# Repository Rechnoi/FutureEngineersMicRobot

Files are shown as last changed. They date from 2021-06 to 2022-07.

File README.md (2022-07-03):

# Команда Violet
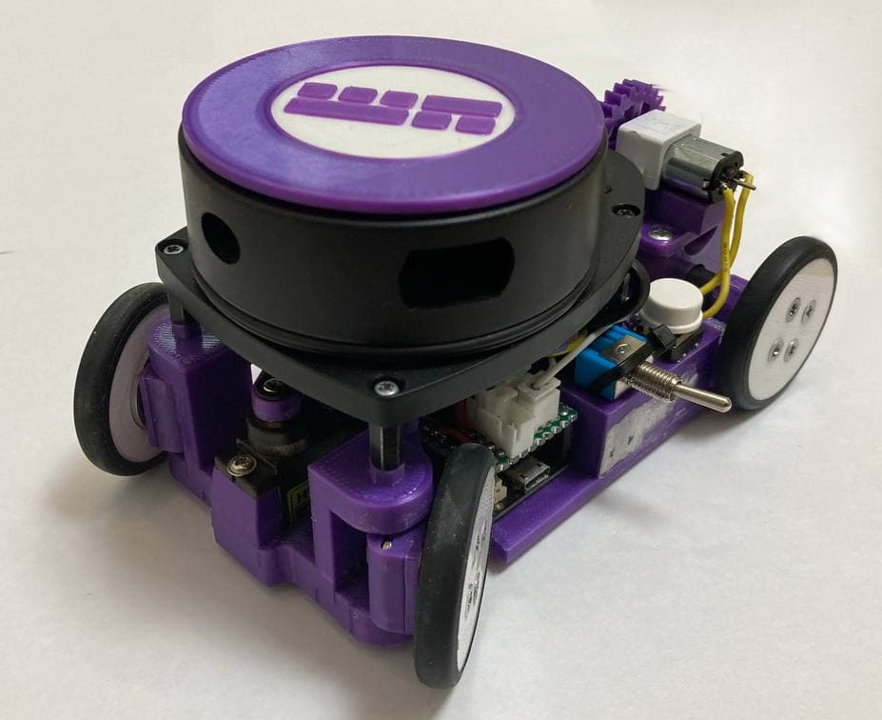
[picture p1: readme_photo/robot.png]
General


### Робот, созданный для решения задачи WRO FutureEngineers 2022 (Version Mk. IV)
### © Антон Иванченко, Александр Широковских, Дмитрий Шмелёв

<br>

## Наш видеообзор на [Youtube](https://youtu.be/LUYHc2npUGY)

<br>

## Введение
  Перед нами стояла задача спроектировать и собрать беспилотное транспортное средство, которое могло бы верно и точно выполнить задачу WRO FutureEngineers 2022. Для достижения поставленных целей мы построили четырехколесного робота на базе ESP32. Основными датчикомами этого робота стали лидар и камер, которые дают информацию о расстоянии до объектов вокруг робота и цвете знаков перед роботом. При разработке были учтены геометрические особенности транспортных средств, такие как углы Аккермана и дифференциальная передача момента.

## Содержание репозитория
  - Папка "3D-models" содержит все версии робота
  - Папка "final/main" содержит код финального заезда
  - Папка "qual/main" содержит код для квалификационного заезда
  - Папка "schematic" содержит электромеханическую схему робота
  - Папка "team_photo" содержит два фото команды по регламенту
  - Папка "robot_photo" содержит обзорные фото робота с шести сторон
  - Папка "readme_photo" содержит фото, используемые в README.md файле

## Фото робота
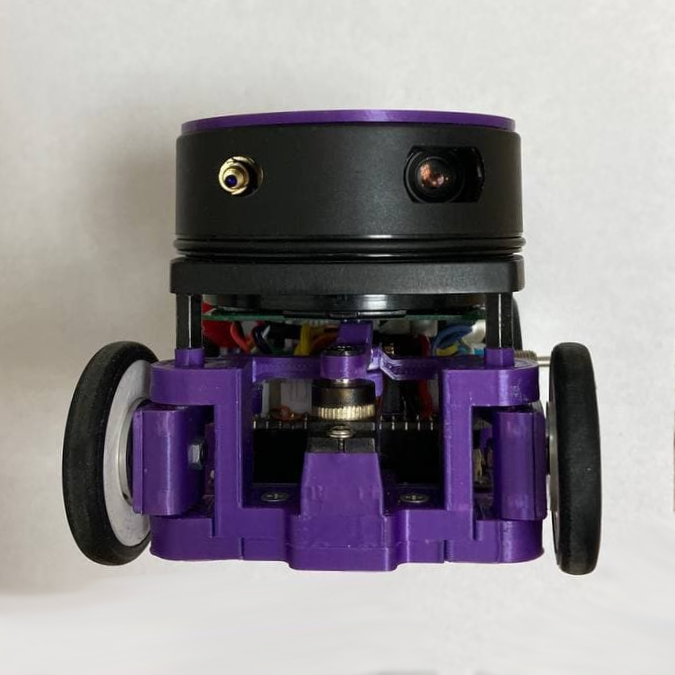
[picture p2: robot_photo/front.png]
Front
  
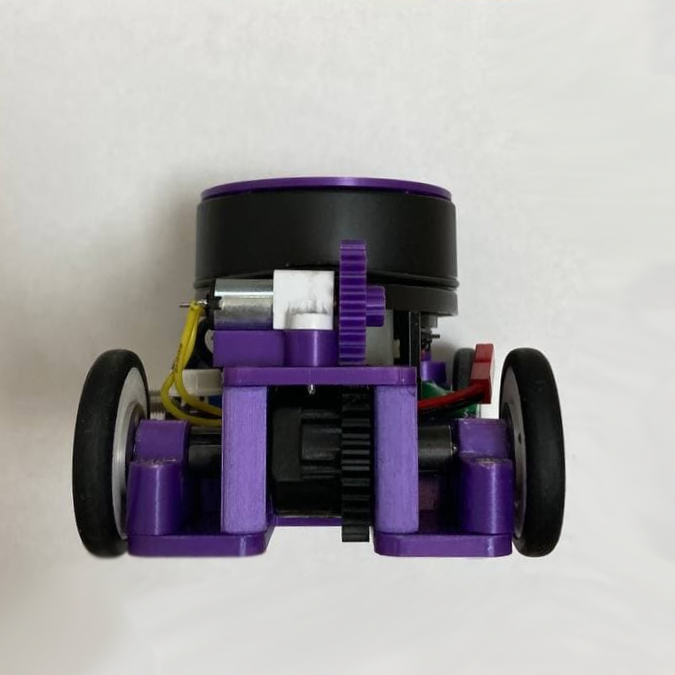
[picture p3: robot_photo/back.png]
Back
  
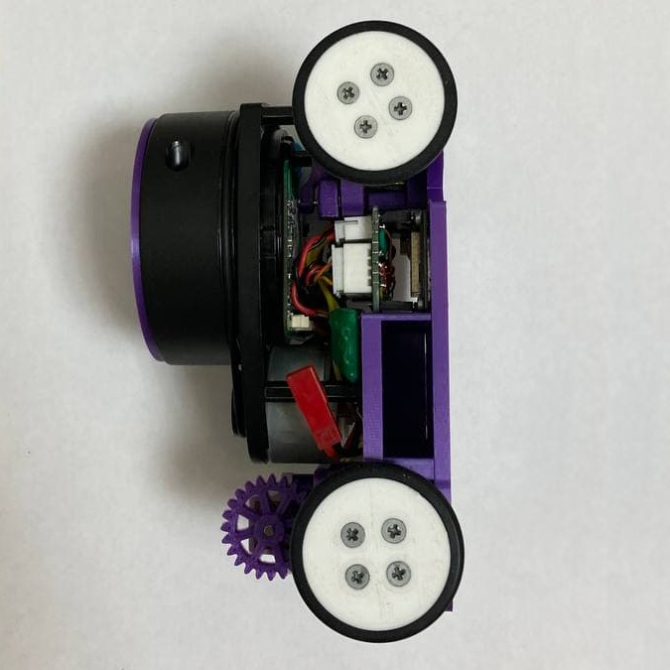
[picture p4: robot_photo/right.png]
Right
  
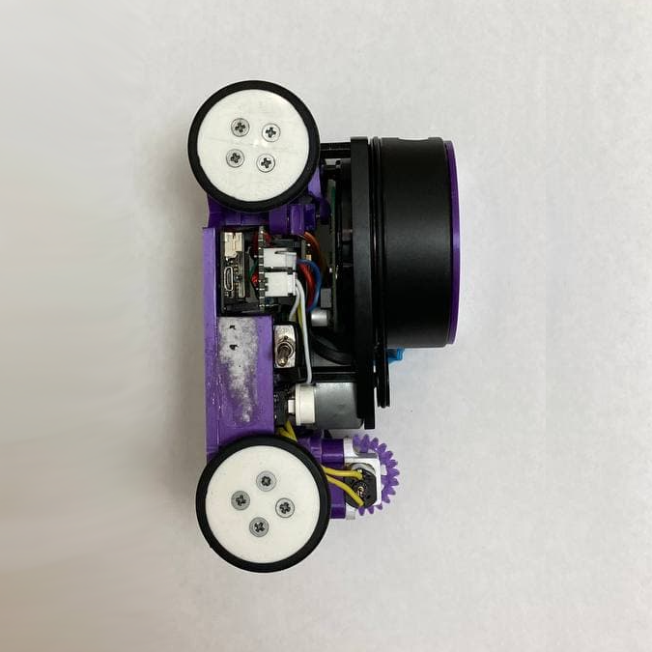
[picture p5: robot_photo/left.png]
Left
  
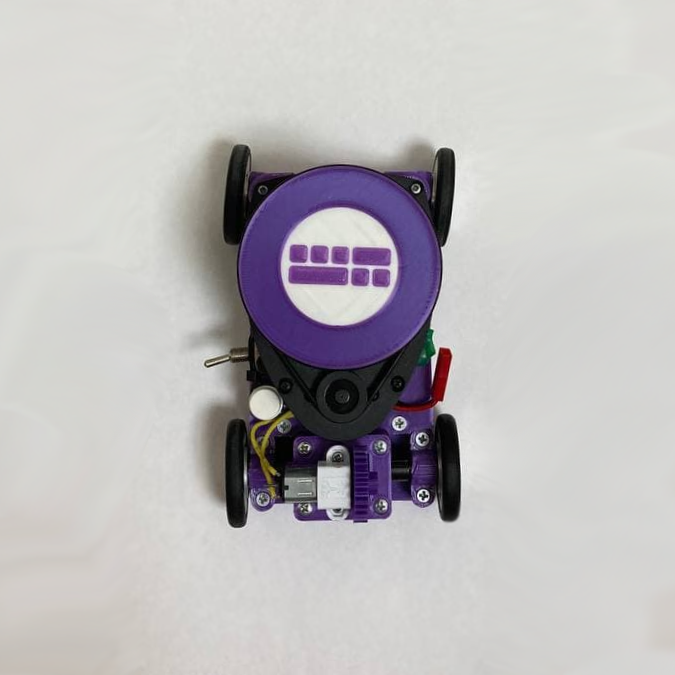
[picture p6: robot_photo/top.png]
Top
  
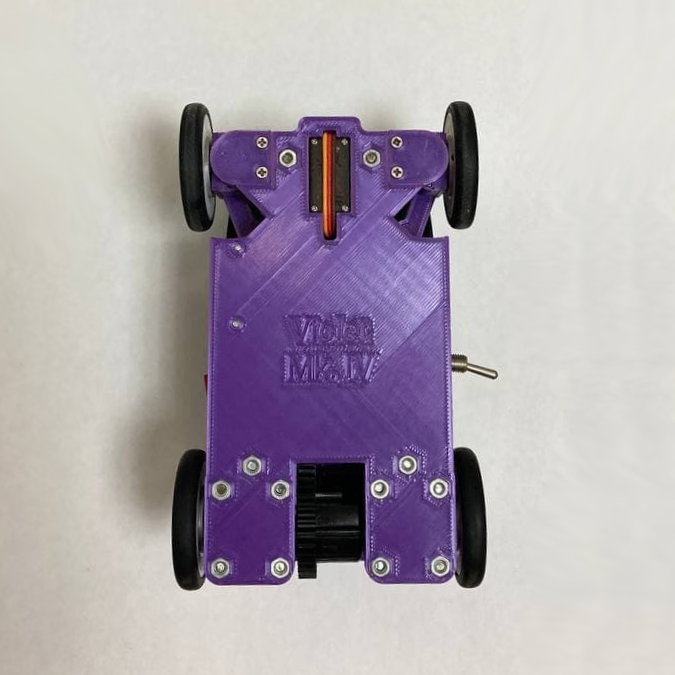
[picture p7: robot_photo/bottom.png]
Bottom
  
  
  *Если картинки не открываются, проверьте папку "robot_photo", пожалуйста

## Схема электромеханического устройства
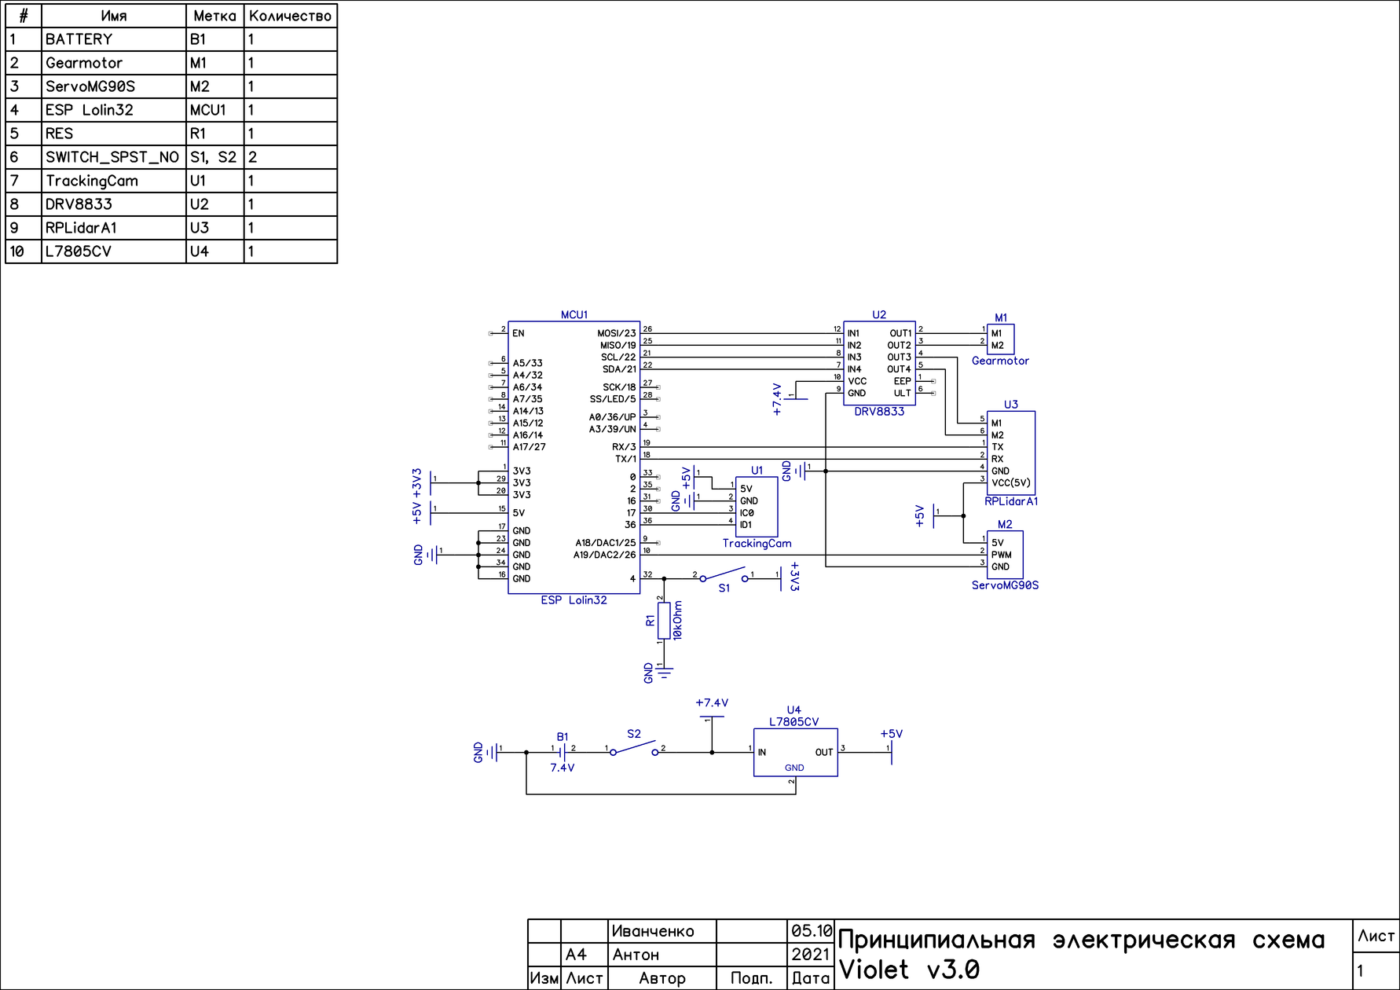
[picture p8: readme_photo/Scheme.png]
Схема
  
  
  *Если картинка не открывается или вам нужна картинка лучшего качества, проверьте папку "schematic", пожалуйста.

## Сборка робота
  - Сначала вам нужно напечатать все необходимые части робота. Для этого зайдите в папку "3D-models/RRO 2021 Mk. IV/STL" и распечатайте все модели на 3D-принтере.
  - Во-вторых, вам нужно купить все необходимые компоненты: [лидар](https://www.slamtec.com/en/Lidar/A1), [камеру](https://robotgeeks.ru/collection/komplektuyuschie-dlya-avtonomnyh-robotov/product/modul-tehnicheskogo-zreniya-trackingcam), [мотор](https://www.pololu.com/product/3042), [сервопривод](https://aliexpress.ru/item/1005002235406689.html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,searchweb201602_,searchweb201603_), [драйвер мотора](https://mcustore.ru/store/moduli/drajver-dvigatelya-drv8833/) и [плату ESP Lolin32](https://mcustore.ru/store/espressif-systems/wemos-loin32-sovmestimyj-kontroller-pod-akkumulyator/), а также компоненты, задействованные в печатной плате робота. Для робота также необходимы 4 подшипника 3x8x3, 2 подшипника 3x8x4, латунные втулки 3x5x4, [дифференциал](https://rc-today.ru/product/differencial-hsp-60065/) и четыре силиконовые [шины Pololu](https://www.pololu.com/product/3408). Для питания робота можно использовать любую 7.4V 2S Li-Po батарею размером 53x30x11.5мм, например, мы используем вот эту [батарею](https://rc-go.ru/cat/akkumulyator-gensace-lipo-7-4v-2s-25c-450mah/).  
  - В-третьих, для сборки напечатаных и купленных компонентов понадобится 12 гаек M3 и 10 гаек М2 гаек и следующие винты(размер указан от головки до конца резьбы):
    - 2xM3 7.6мм (с потайной головкой)
    - 2xM3 20.8мм (с потайной головкой)
    - 2xM3 16.25мм (с потайной головкой)
    - 4xM3 16.25мм (с потайной головкой)
    - 16xM3 6.5мм (с потайной головкой)
    - 4xM3 33.8мм
    - 2xM2 7мм
    - 2xM2 8.8мм
    - 8xM2 6,5мм (с потайной головкой)
    - 6xM2 10мм (с потайной головкой)
  - В-четвертых, в соответствии со схемой, необходимо иметь макетную плату размером не более 55,8x25,4 мм. Рекомендуется использовать штырьевой разъем и гребенку-гнездо для удобства замены сгоревших компонентов. Плата управления должна быть собрана в следующем порядке: ESP Lolin32, плата шилда и драйвер.
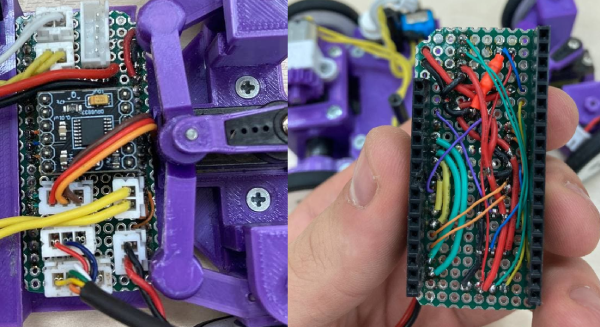
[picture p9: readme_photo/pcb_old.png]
PCB_old
  
  - В-пятых, открыв в Inventor файл-сборку "3D-models/RRO 2021 Mk. IV/Робот RRO 2021 Mk. IV.iam", соберите робота, как показано на модели.

## О наших электрических и механических компонентах
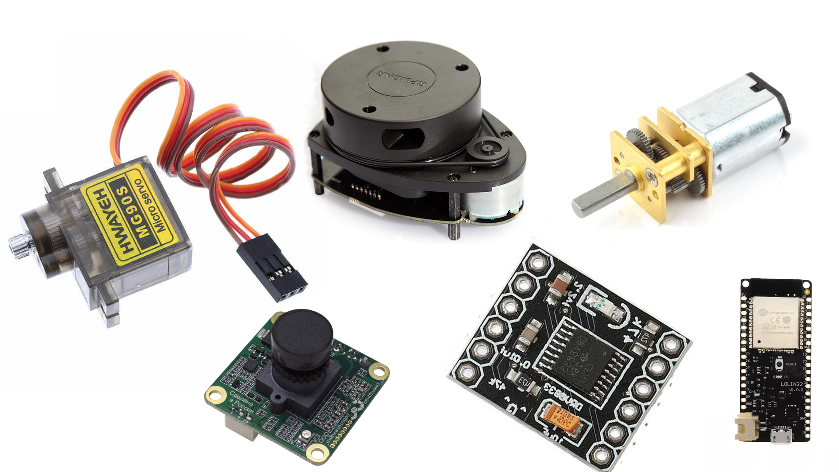
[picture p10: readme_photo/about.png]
About

### Лидар
  В нашем роботе используется RPLidar A1. Он основан на принципе лазерной триангуляции расстояния и использует высокоскоростной процессор для сбора и обработки данных, разработанный компанией Slamtec. Система измеряет данные о расстоянии более 4500 раз в секунду. Дальномер RPLidar A1 вращается по часовой стрелке и выполняет 360-градусное лазерное сканирование окружающего пространства. Полученные данные преобразуются главным микроконтроллером для построения виртуальных стен.

### Камера
  В этом году для определения цвета знаков мы решили использовать модуль технического зрения TrackingCam. Он является сенсорным устройством для исследования окружающего пространства путем обработки и анализа изображения со встроенной видеокамеры. Модуль является отечественной разработкой.

### ESP32
  Плата Lolin D32 основана на микроконтроллере ESP32 от "Espressif systems" с низким энергопотреблением. Она обладает множеством мощных функций, включая двухъядерный процессор на базе Arm, Wi-Fi, Bluetooth, I2C, I2S, SPI, АЦП, ЦАП и 4 Мб флэш-памяти. Модуль D32 предоставляет эти функции в удобном формате DIP и может быть запрограммирован непосредственно с USB-интерфейса - дополнительное оборудование для программирования не требуется.

### DRV8833
  Для управления двигателями используется драйвер DRV8833, который позволяет управлять двумя коллекторными двигателями одновременно. Внутри микросхема драйвера содержит два независимых Н-моста, рассчитанных на напряжение от 2,7 до 10,8 В, с рабочим током каждого канала до 0,5 А без радиатора или до 1,5 А с установленным на микросхеме радиатором.

### Металлический мотор-редуктор Polulu
  Этот мотор-редуктор представляет собой миниатюрный двигатель постоянного тока средней мощности с обмоткой на 6 В и металлическим редуктором. Его поперечное сечение составляет 10 × 12 мм, а D-образный выходной вал редуктора имеет длину 9 мм и диаметр 3 мм.
  Эти миниатюрные щеточные моторы-редукторы постоянного тока выпускаются в широком диапазоне передаточных чисел - от 5:1 до 1000:1 - и с пятью различными двигателями: мощными 6 В и 12 В с угольными щетками с длительным сроком службы (HPCB), а также двигателями высокой (HP), средней (MP) и малой (LP) мощности 6 В с щетками из драгоценных металлов с меньшим сроком службы. Двигатели HPCB на 6 В и 12 В обладают одинаковой производительностью при соответствующих номинальных напряжениях, только двигатель на 12 В потребляет вдвое меньше тока, чем двигатель на 6 В. В нашем роботе используется двигатель 250:1 HPCB на 6 В.

### Сервопривод MG90S
  MG90S - это маленький сервопривод похожий на популярную версию MG90. Так почему мы не использовать его синий аналог? Ответ прост - металлический редуктор. Благодаря им сервопривод может приложить большое усилие для поворота колес без каких-либо последствий. С помощью этого сервопривода робот может довольно точно задать угол поворота колес. 

## Установка необходимых программ и прошивка платы

  - Для программирования робота вам понадобится [Arduino IDE](https://www.arduino.cc/en/software). Это программное обеспечение с открытым исходным кодом позволяет легко писать код и загружать его в плату. Откройте exe-файл и следуйте инструкциям программы установки.

  - Установите ESP32 в менеджере плат Arduino IDE, добавив ссылку (https://dl.espressif.com/dl/package_esp32_index.json) в настройки IDE.
    - Сначала добавьте дополнительные ссылки менеджера плат
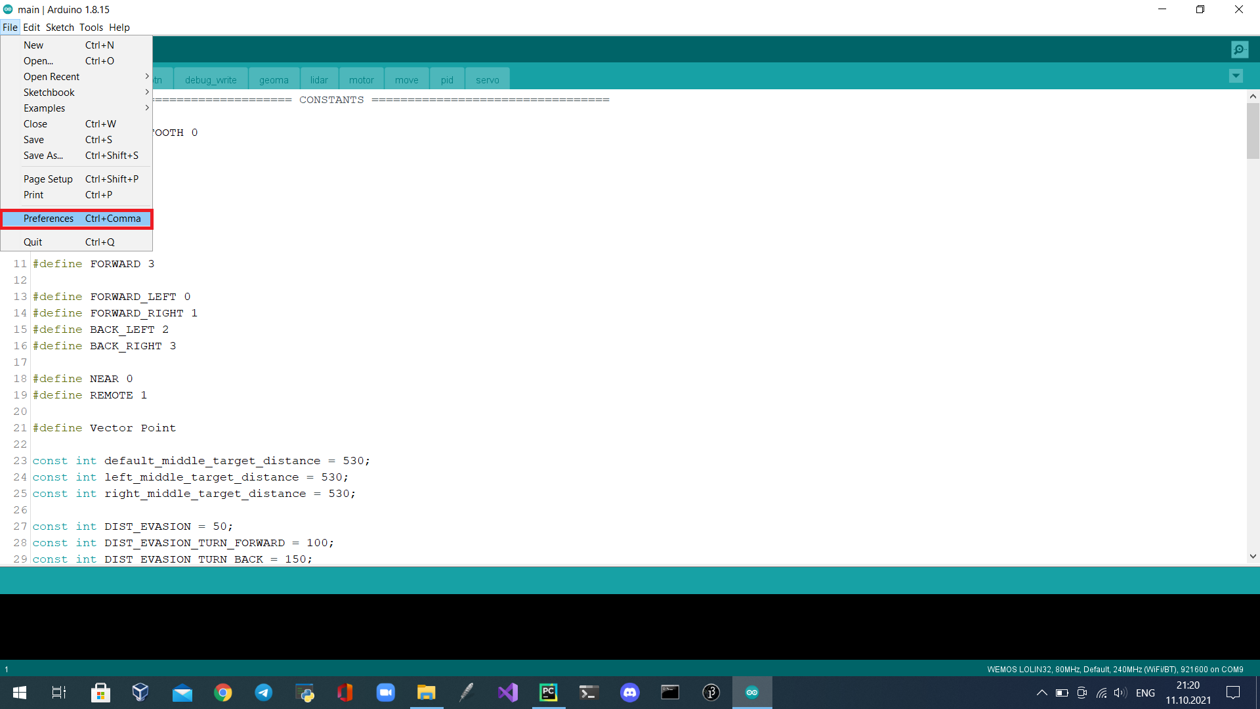
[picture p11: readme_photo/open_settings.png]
Settings
    
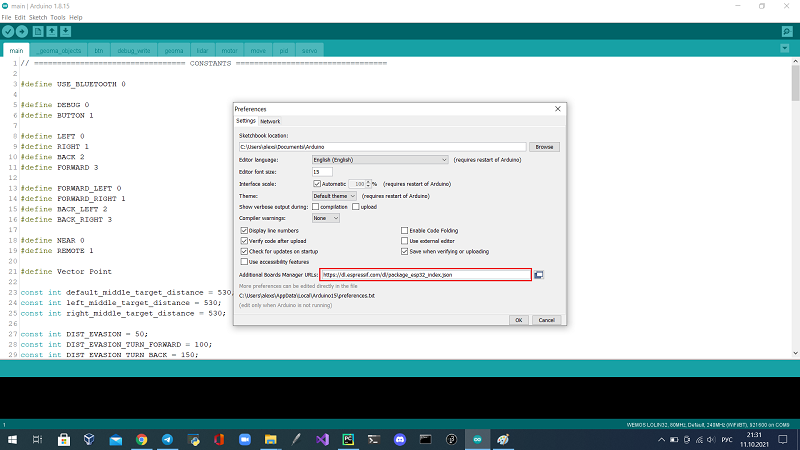
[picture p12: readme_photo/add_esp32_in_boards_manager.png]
Менеджер
    
    - Во-вторых, установите плату
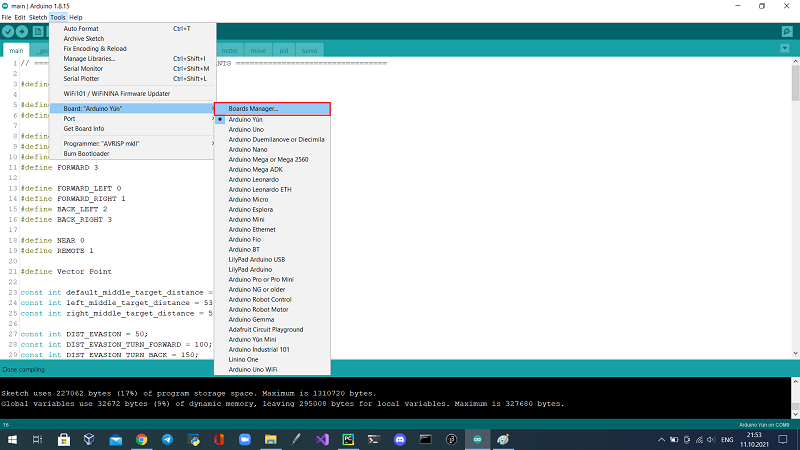
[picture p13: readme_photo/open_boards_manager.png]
Boards
    
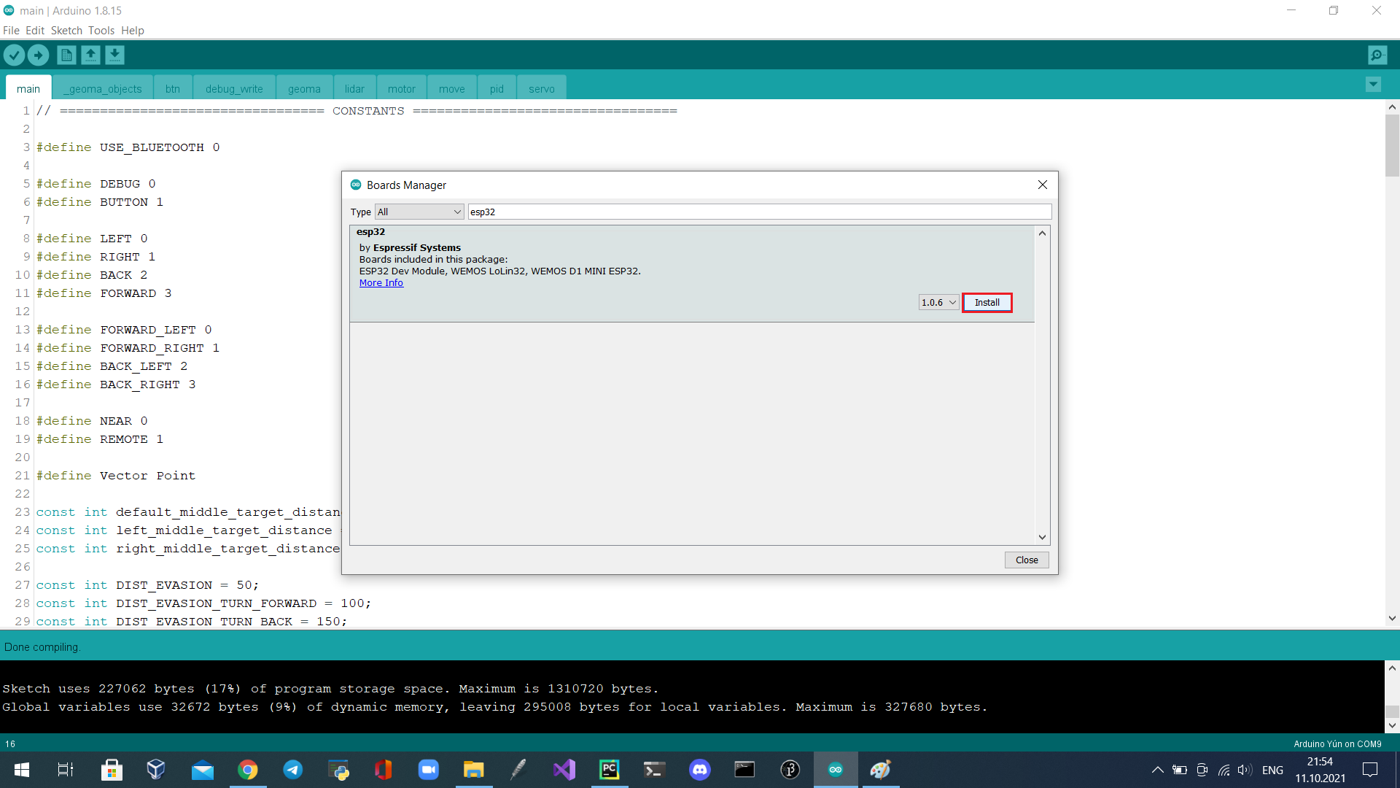
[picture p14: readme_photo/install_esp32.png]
Install
    
  - Используйте менеджер библиотек для установки библиотек ESP32.
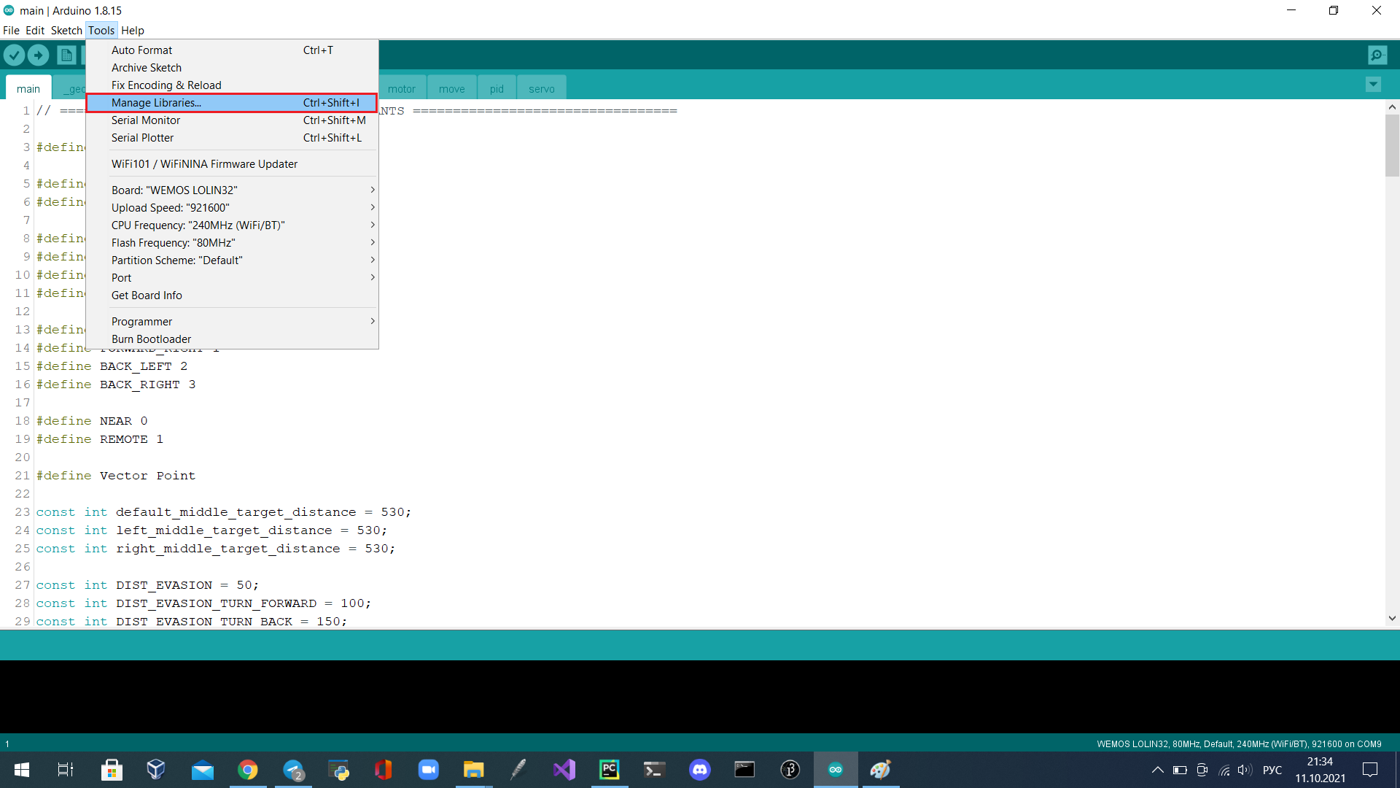
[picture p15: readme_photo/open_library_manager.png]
Открыть
  
    - Библиотеку для аналогового порта ESP32.
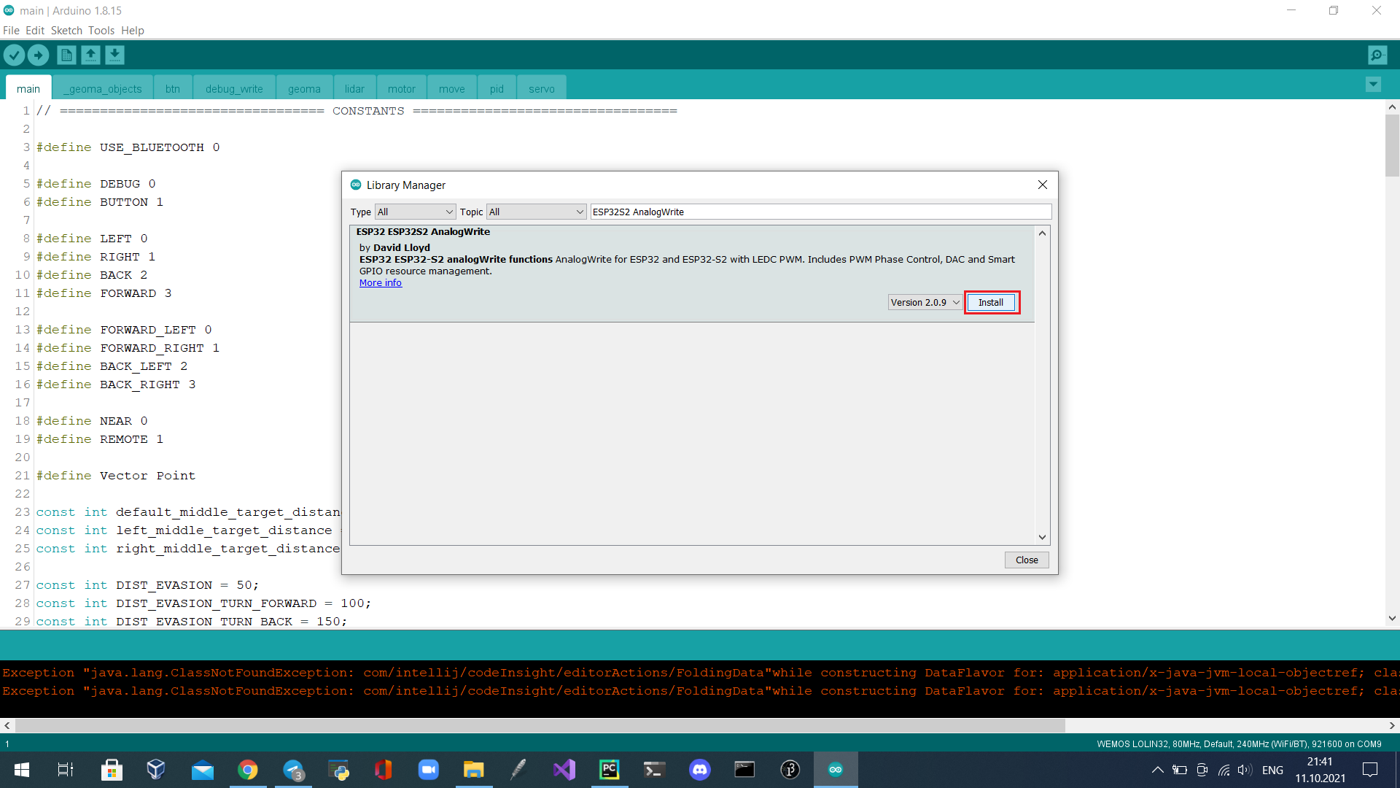
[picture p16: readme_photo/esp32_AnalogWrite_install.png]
AnalogWrite
    
    - И библиотеку ESP32Servo.
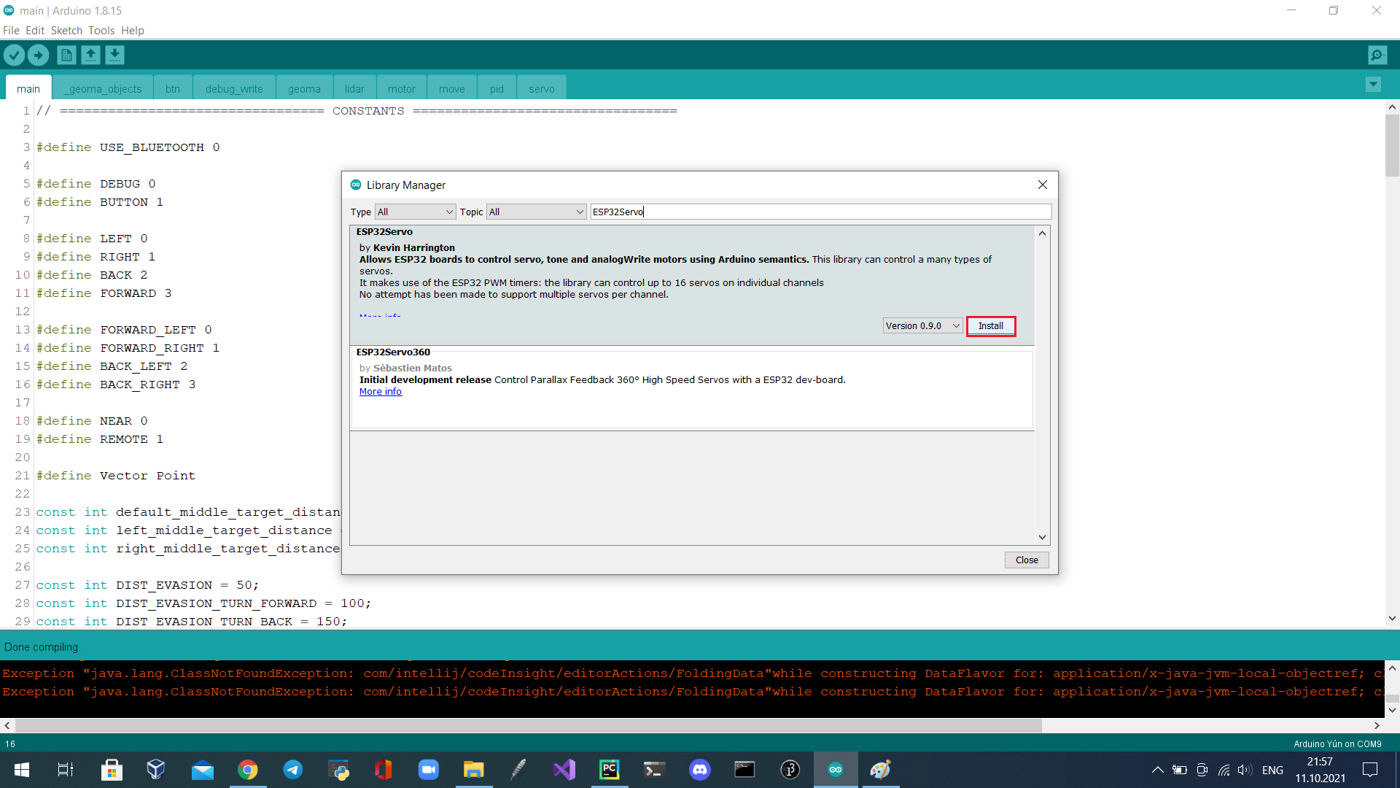
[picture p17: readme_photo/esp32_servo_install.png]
ESP32Servo
    
  - Выберите плату "WEMOS LOLIN32". Подключите плату ESP32 с помощью кабеля microUSB к компьютеру и выберите соответствующий порт в IDE arduino. Нажмите кнопку "Загрузить".
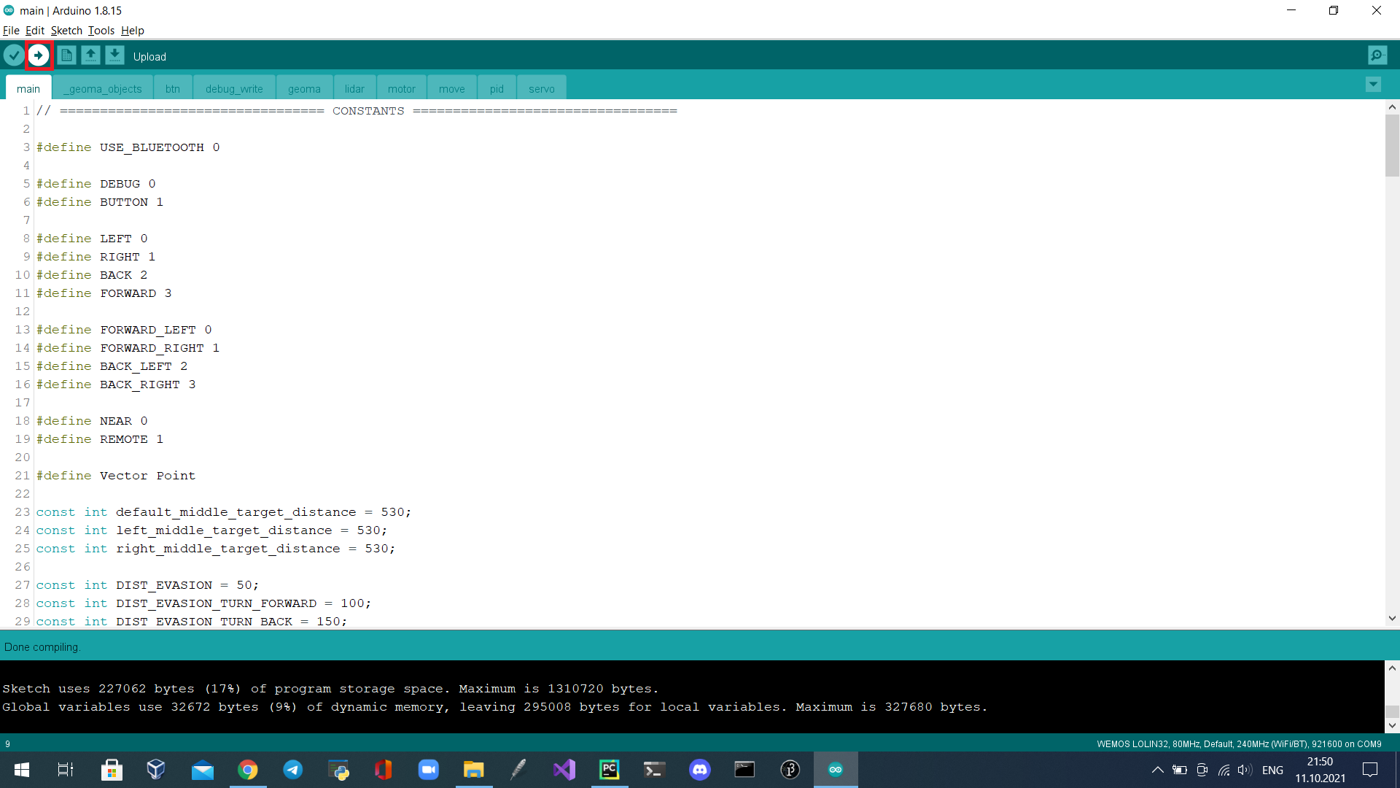
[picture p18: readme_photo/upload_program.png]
Upload
  

## Запуск робота

 - Загрузить в робота нужный код (в зависимости от раунда, квалификации или финала)
 - Включите робота с помощью тумблера.
 - Проведите жеребьевку, как указано в правилах
 - Поставьте робота на стартувую позицию
 - Нажмите кнопку для запуска

 ## Наши планы на будущее

  Как всегда, на все не хватает времени, а идеи появляются часто. Поэтому мы создали этот раздел с нашими планами.

  - ### Поменять плату, созданную на макетной плате, на плату, созданную на заводе.
    Для этой идеи мы немного изменили принципиальную схему робота, а также создали макет самой платы. Осталось только дождаться готовую плату с завода и протестировать ее.
    
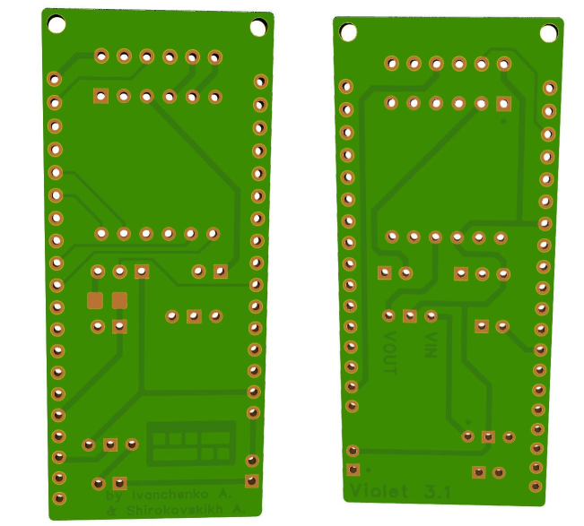
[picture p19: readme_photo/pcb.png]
Lidar
    
  
  - ### Создание носового обтекателя и работа над аэродинамикой робота
    Эта идея пришла, когда нам нужно было ускорить робота. В итоге мы не стали рассматривать его как очень сложный вариант и оставили на будущее, но обтекаемая форма робота дает плюсы к устойчивости, что является приоритетом. 

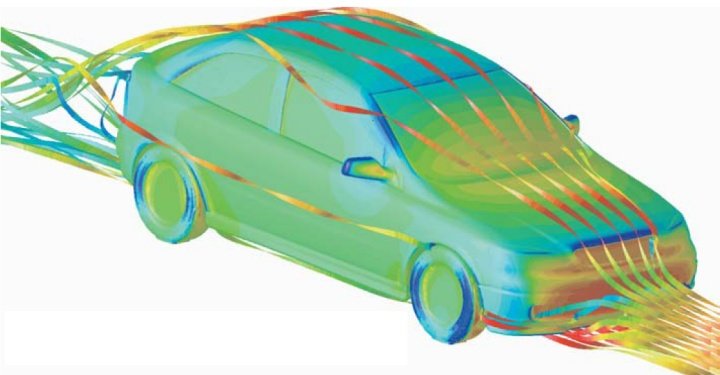
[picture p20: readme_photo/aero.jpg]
Aero
    

  - ### Сделать робота еще меньше
    От регионального этапа до всероссийского размер робота уменьшился почти в три раза. Но мы уверены, что это не предел и можно уменьшить конструкцию ещё. Небольшой размер робота позволяет нам не делать лишних маневров на трассе, что ускоряет время прохождения.

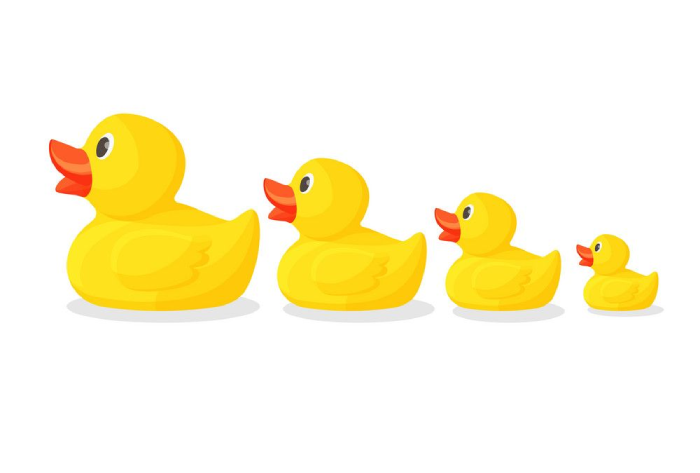
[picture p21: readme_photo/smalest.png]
Ducks


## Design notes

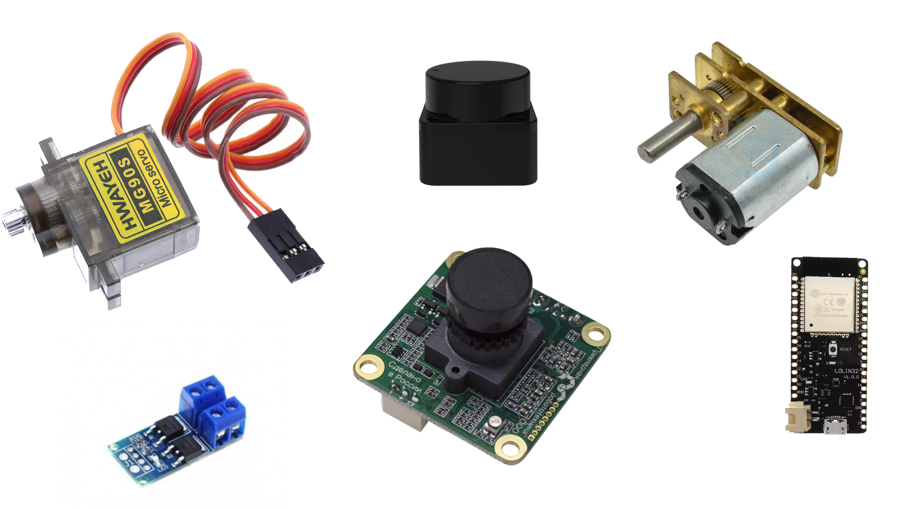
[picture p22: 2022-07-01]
readme_photo/about1.png

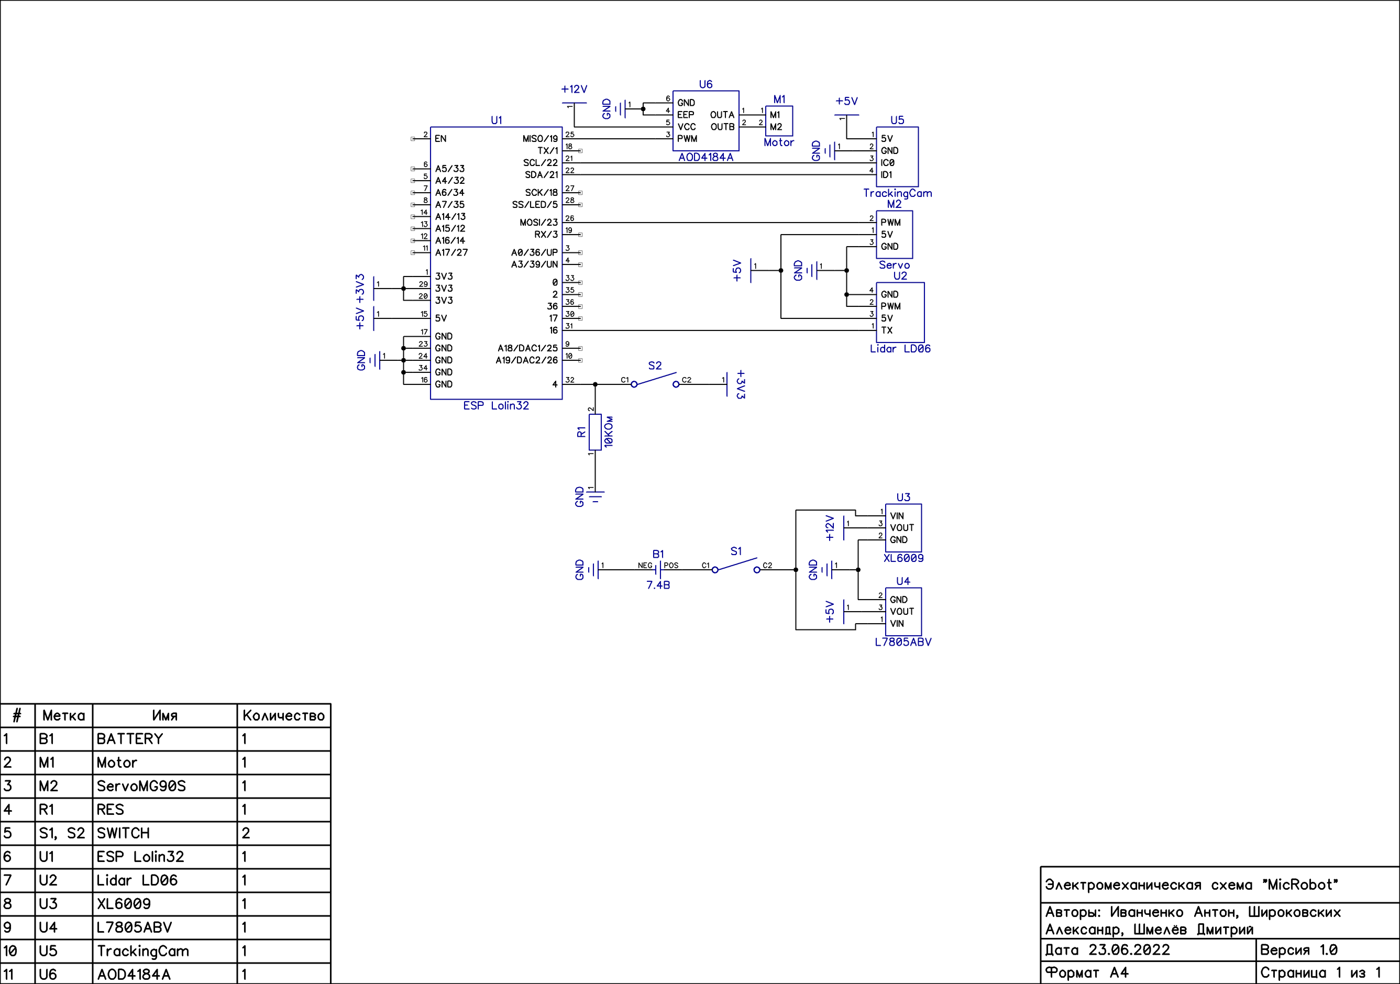
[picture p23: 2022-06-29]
readme_photo/Scheme1.png

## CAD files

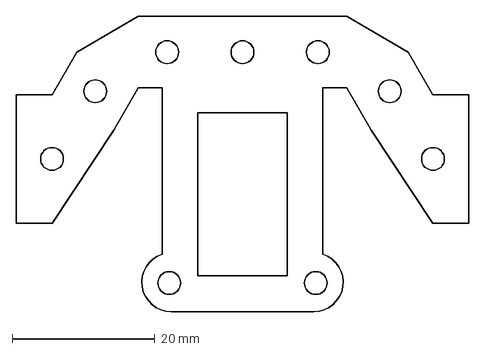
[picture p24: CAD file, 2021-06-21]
3D-models/RRO 2021 Mk. I/Blueprints/Грань основы рулевого управления.dxf
63.3 x 41.3 mm

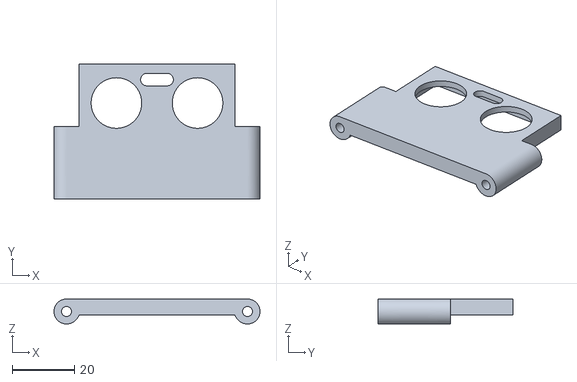
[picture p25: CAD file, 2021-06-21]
3D-models/RRO 2021 Mk. I/STL/Крепление ультрасоника.stl
66.0 x 43.2 x 8.00

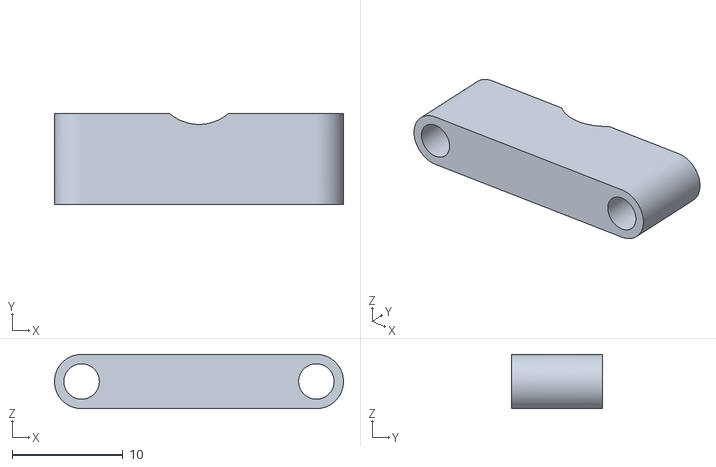
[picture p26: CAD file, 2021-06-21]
3D-models/RRO 2021 Mk. I/STL/Новая папка (10)/Стойка подшипника 3мм.stl
26.1 x 8.25 x 4.90

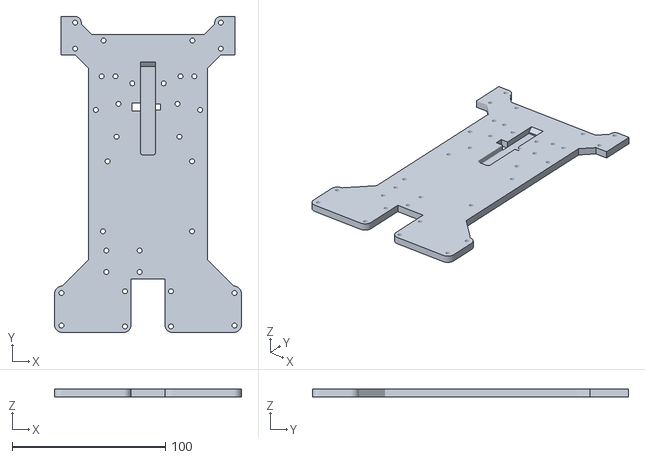
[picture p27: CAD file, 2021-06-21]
3D-models/RRO 2021 Mk. I/STL/Новая папка (11)/Основа робота.stl
122.1 x 206.3 x 5.00

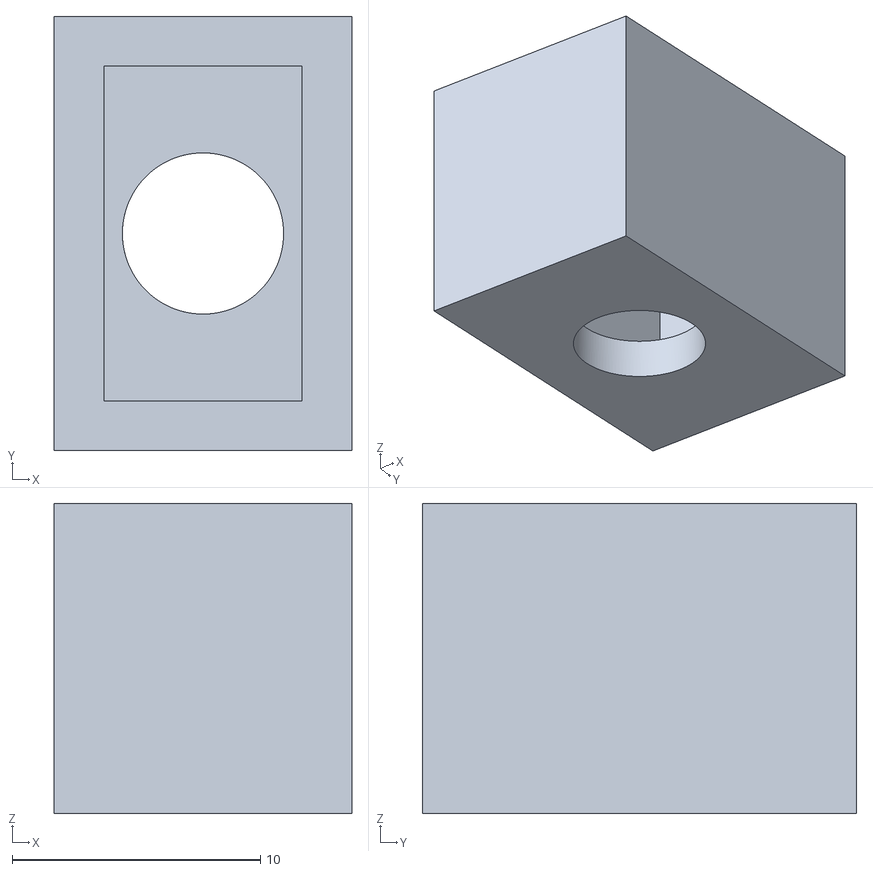
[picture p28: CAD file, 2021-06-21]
3D-models/RRO 2021 Mk. I/STL/Новая папка (12)/Деталь1.stl
12.0 x 17.5 x 12.5

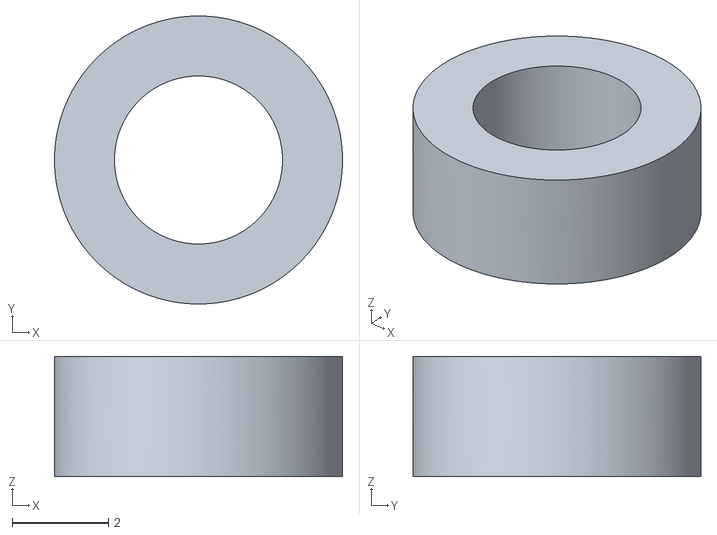
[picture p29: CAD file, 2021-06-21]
3D-models/RRO 2021 Mk. II/STL/Новая папка/Стойки камеры.stl
6.00 x 6.00 x 2.50

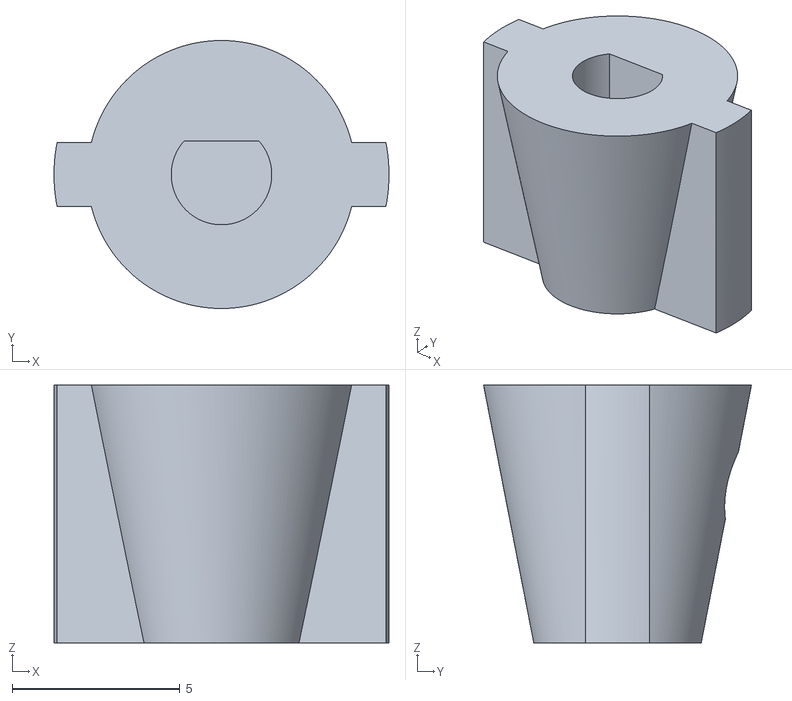
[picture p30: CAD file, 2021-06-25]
3D-models/RRO 2021 Mk. III/Body/Новая папка (2)/Переходник с дифференциала на ось 3мм.stl
10.0 x 8.00 x 7.70

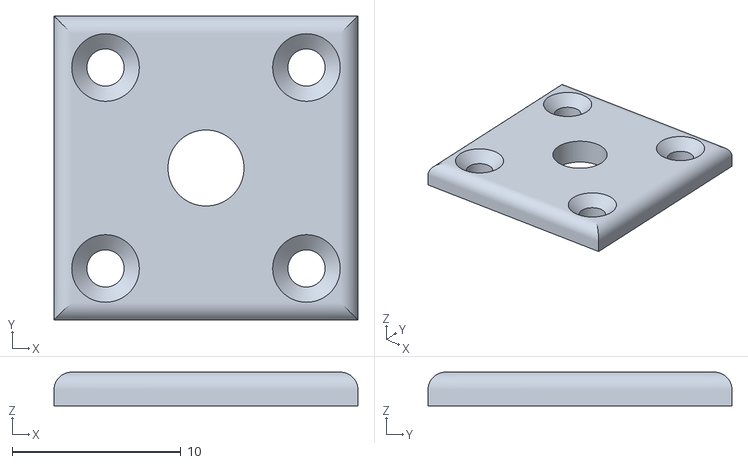
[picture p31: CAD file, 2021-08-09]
3D-models/RRO 2021 Mk. III/STL/Новая папка (10)/Крышка поворотного кулака.stl
18.0 x 18.0 x 2.00

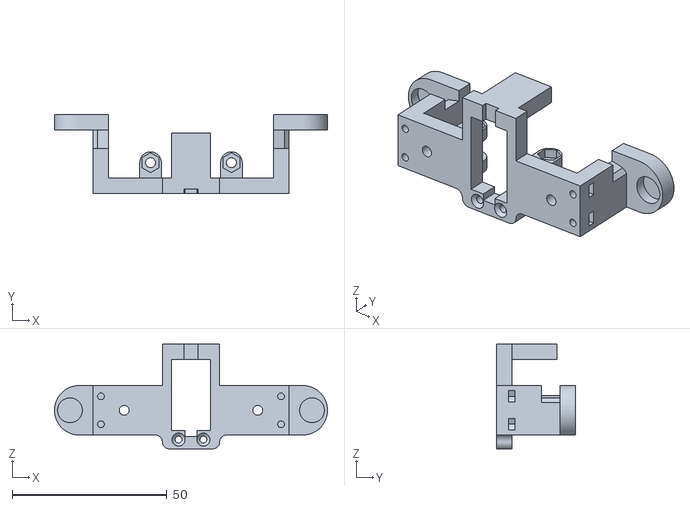
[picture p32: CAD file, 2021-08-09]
3D-models/RRO 2021 Mk. III/STL/Новая папка (11)/Основа рулевого механизма.stl
88.1 x 25.6 x 33.8

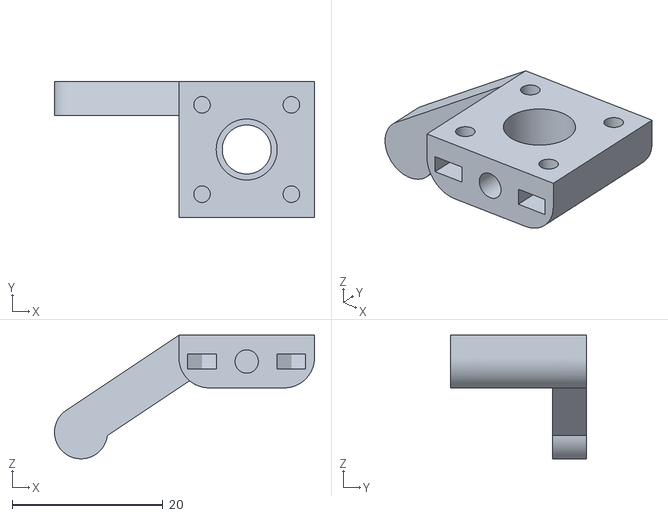
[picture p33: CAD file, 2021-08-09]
3D-models/RRO 2021 Mk. III/STL/Новая папка (13)/Деталь крепления диска к поворотному механизму_ЗЕРКАЛО1.stl
34.5 x 18.0 x 16.4

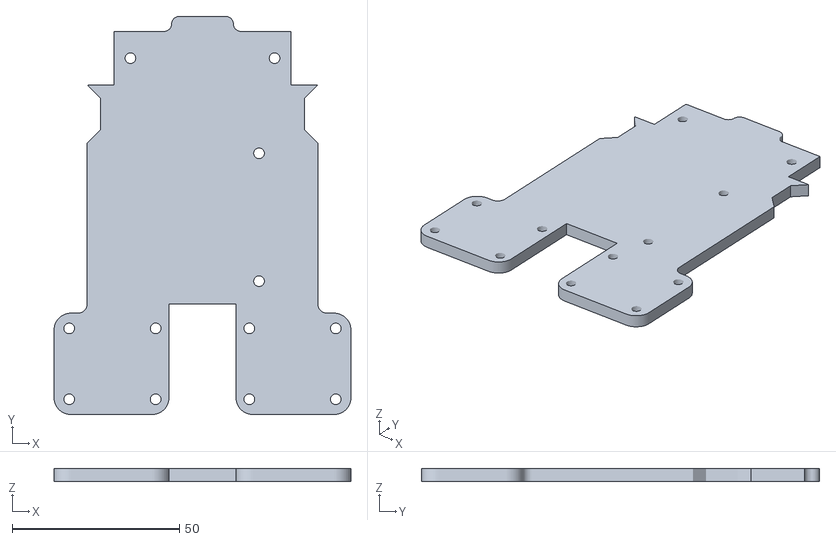
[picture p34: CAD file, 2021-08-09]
3D-models/RRO 2021 Mk. III/STL/Новая папка (14)/Основа робота.stl
88.8 x 119.0 x 4.00

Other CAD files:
3D-models/RRO 2021 Mk. I/Test/Деталь11.dwg
3D-models/RRO 2021 Mk. II/Test/Деталь11.dwg
3D-models/RRO 2021 Mk. III/STL/Новая папка/Деталь крепления диска к поворотному механизму.stl
3D-models/RRO 2021 Mk. I/Body/OldVersions/Балка рулевого управления ведомая.0006.ipt
3D-models/RRO 2021 Mk. I/Body/OldVersions/Балка рулевого управления ведущая.0012.ipt
3D-models/RRO 2021 Mk. I/Body/OldVersions/Балка рулевого управления ведущая.0016.ipt
3D-models/RRO 2021 Mk. I/Body/OldVersions/Балка рулевого управления.0001.ipt
3D-models/RRO 2021 Mk. I/Body/OldVersions/Балка рулевого управления.0002.ipt
3D-models/RRO 2021 Mk. I/Body/OldVersions/Ведущая шестерня дифференециала.0003.ipt
3D-models/RRO 2021 Mk. I/Body/OldVersions/Втулка между подшипниками рулевого управления.0002.ipt
3D-models/RRO 2021 Mk. I/Body/OldVersions/Деталь крепления диска к поворотному механизму.0015.ipt
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

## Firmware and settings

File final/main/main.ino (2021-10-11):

// ================================= CONSTANTS =================================

#define USE_BLUETOOTH 0

#define DEBUG 0
#define BUTTON 1

#define LEFT 0
#define RIGHT 1
#define BACK 2
#define FORWARD 3

#define FORWARD_LEFT 0
#define FORWARD_RIGHT 1
#define BACK_LEFT 2
#define BACK_RIGHT 3

#define NEAR 0
#define REMOTE 1

#define Vector Point

const int default_middle_target_distance = 530;
const int left_middle_target_distance = 530;
const int right_middle_target_distance = 530;

const int DIST_EVASION = 50;
const int DIST_EVASION_TURN_FORWARD = 100;
const int DIST_EVASION_TURN_BACK = 150;

// ============================= GEOMETRIC OBJECTS =============================

struct Point {
    int16_t x;
    int16_t y;

    Point();
    Point(int16_t x, int16_t y);

    int getSqrLen() const;
    double getLen() const;
    Vector getPerp() const;

    Point operator - () const;
};

// The line is given by the equation A * x + B * y + C = 0
struct Line {
    int A;
    int B;
    int C;

    Line();
    Line(const Point& A, const Point& B);
    
    double getX(int16_t y) const;
    double getY(int16_t x) const;
    
    double distToCenter() const;
    int sqrDistToPoint(const Point& P) const;
    int distToPoint(const Point& P) const;
};

struct Segment {
    Point A;
    Point B;
    Line line;

    Segment();
    Segment(const Point& A, const Point& B);

    void clear();
    bool empty() const;

    Vector getVector() const;
};

// ================================= VARIABLES =================================

bool side_move_forward;
int16_t dir_rotate;

int middle_target_distance;
int target_distance;

int cnt_signs;
int cnt_good_signs;

int cnt_rotates;

bool exist_signs[2][4];

Point signs[100];

bool is_sign[2][3];
bool is_rotate_sign[2][2];

double pid_error;
double pid_value;

const int MAX_CNT_POINTS = 2000;

Point points[MAX_CNT_POINTS];
int cnt_points;

int cnt_segments;

int16_t buff[4000];

Segment border[4];

bool pid_is_ready;
bool turnover_is_ready;

bool begin_pid_move;

// ================================= FUNCTIONS =================================


int time_turnover;

unsigned long long time_begin;
int diff_turnover;
unsigned long long time_old_turnover;

// Processing of information received during lidar turnover
void processingTurnover() {
    diff_turnover = millis() - time_old_turnover;
    time_old_turnover = millis();
    time_begin = millis();
    splitComponent();
    
    if (dir_rotate == -1) {
        for (int dir = 0; dir < 2; ++dir) {
            if (!border[dir].empty()) {
                if (border[dir].line.distToCenter() > 1500) {
                    dir_rotate = dir;
                }
                Segment seg = border[dir];
                Vector v = seg.getVector();
                if (v.y < 0) {
                    v = -v;
                }
                int cnt[2] = {0, 0};
                for (int i = 0; i < cnt_points; ++i) {
                    int dist = seg.line.distToPoint(points[i]);
                    if (dist > 100) {
                        if ((seg.A ^ points[i]) * v > 0) {
                            ++cnt[RIGHT];
                        } else {
                            ++cnt[LEFT];
                        }
                    }
                }
                if (cnt[dir] >= 3) {
                    dir_rotate = dir;
                }
            }
        }
    }
    pid_is_ready = !border[side_move_forward].empty();
    turnover_is_ready = true;
    time_turnover = millis() - time_begin;
    if ((pid_is_ready) && ((!border[FORWARD].empty()) || (!border[BACK].empty()))) {
        for (int i = 0; i < cnt_signs; ++i) {
            processingSign(signs[i]);
        }
        updateTargetDistance();
    }
}

// Initializing variables
void initVariables() {
    side_move_forward = RIGHT;
    dir_rotate = -1;
    middle_target_distance = default_middle_target_distance;
    target_distance = middle_target_distance;
    cnt_rotates = 0;

    
    pid_is_ready = false;
    turnover_is_ready = false;
    begin_pid_move = true;

    cnt_points = 0;
    cnt_segments = 0;

    pid_value = 0;
    time_turnover = 0;

    memset(is_sign, 0, 6);
    memset(is_rotate_sign, 0, 4);
    memset(exist_signs, 0, 8);
}

void setup() {}

void loop() {
    initVariables();
#if DEBUG
    debugWriteSetup();
#endif
    servoSetup();
    motorSetup();
    lidarSetup();

#if BUTTON
    btnSetup();
    while (!btnReadState()) {
        lidarRead();
    }
#endif
    unsigned long long time_begin = millis();
    while (millis() - time_begin < 500) {
        lidarRead();
    }
    dir_rotate = -1;
    memset(is_sign, 0, 6);
    memset(is_rotate_sign, 0, 4);
    time_begin = millis();
    while (millis() - time_begin < 500) {
        lidarRead();
    }
    
    solve();
#if !DEBUG
    while (true) {}
#endif
    delay(2000);
}

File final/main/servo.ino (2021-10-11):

#include <ESP32Servo.h>

const int port_servo = 26;

const int CENTER_ANGLE = 98;
const int MAX_SERVO_ANGLE = 50;
const int TURN_ANGLE = 30;

Servo servo;

// Initializing the servo
void servoSetup() {
    ESP32PWM::allocateTimer(2);
    servo.attach(port_servo);
    servoTurnCenter();
}

// Turning the servo to the center
void servoTurnCenter() {
    servo.write(CENTER_ANGLE);
}

// Rotation of the servo by a given angle
void servoWrite(int angle) {
    if (angle < -MAX_SERVO_ANGLE) {
        angle = -MAX_SERVO_ANGLE;
    } else if (angle > MAX_SERVO_ANGLE) {
        angle = MAX_SERVO_ANGLE;
    }
    angle = CENTER_ANGLE - angle;
    servo.write(angle);
}

// Turning the servo on the turn
void servoTurn(bool dir) {
    if (dir == LEFT) {
        servoWrite(-TURN_ANGLE);
    } else {
        servoWrite(TURN_ANGLE);
    }
}

// Servo angle reading
int servoRead() {
    return CENTER_ANGLE - servo.read();
}

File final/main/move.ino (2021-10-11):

// Riding on the wall
void moveBorder() {
    if (pid_is_ready) {
        pidCalculate();
        servoWrite(round(pid_value));
        pid_is_ready = false;
    } else if (turnover_is_ready) {
        servoWrite(0);
    }
    turnover_is_ready = false;
}

void updateMainTargetDistance() {
    if (side_move_forward == LEFT) {
        middle_target_distance = left_middle_target_distance;
    } else {
        middle_target_distance = right_middle_target_distance;
    }
}

void rotate() {
    if (cnt_rotates < 4) {
        for (int side = 0; side < 2; ++side) {
            for (int i = 0; i < 3; ++i) {
                exist_signs[side][cnt_rotates] |= is_sign[side][i];
            }
        }
    }
    
    servoTurn(dir_rotate);
    
    bool flag = true;
    while (flag) {
        lidarRead();
        if ((!border[BACK].empty()) && (border[BACK].line.distToCenter() < 1500)) {
            Vector v = border[BACK].getVector();
            double angle = abs(atan2(v.y, v.x));
            if (min(angle, PI - angle) < radians(35)) {
                flag = false;
            }
        }
    }
    servoTurnCenter();

    unsigned long long time_begin = millis();

    memset(is_sign, 0, 6);
    memset(is_rotate_sign, 0, 4);
    
    pid_is_ready = false;
    turnover_is_ready = false;
    begin_pid_move = true;
    ++cnt_rotates;
    
    target_distance = middle_target_distance;
    

    while ((border[BACK].empty()) || (border[BACK].line.distToCenter() < 1100)) {
        lidarRead();
        moveBorder();
    }
}

const int dist_to_rotate = 860; //760;

// Riding to the turn
void moveToRotate() {
    bool flag = true;
    while (flag) {
        lidarRead();
        moveBorder();
        if (!border[FORWARD].empty()) {
            if (is_rotate_sign[dir_rotate][NEAR] == is_rotate_sign[dir_rotate][REMOTE]) {
                if (border[FORWARD].line.distToCenter() <= dist_to_rotate) {
                    flag = false;
                }
            } else if (is_rotate_sign[dir_rotate][NEAR] > is_rotate_sign[dir_rotate][REMOTE]) {
                if (border[FORWARD].line.distToCenter() <= dist_to_rotate - DIST_EVASION_TURN_FORWARD) {
                    flag = false;
                }
            } else {
                if (border[FORWARD].line.distToCenter() <= dist_to_rotate + DIST_EVASION_TURN_BACK) {
                    flag = false;
                }
            }
        }
    }
}

// Riding to the first turn
void moveStart() {
    if ((border[LEFT].empty()) || (border[RIGHT].empty())) {
        side_move_forward = !border[RIGHT].empty() ? RIGHT : LEFT;
    } else {
        side_move_forward = border[RIGHT].line.distToCenter() > border[LEFT].line.distToCenter() ? RIGHT : LEFT;
    }
    updateMainTargetDistance();
    
    while (dir_rotate == -1) {
        lidarRead();
        moveBorder();
    }
    if (dir_rotate == side_move_forward) {
        side_move_forward = !side_move_forward;
        updateMainTargetDistance();
    }
    moveToRotate();
    target_distance = middle_target_distance;
}

void moveFinish() {}

// Updating the target distance to the wall
void updateTargetDistance() {
    Point robot = conv_rect_coord(Point(0, 0));
    int i = -1;
    if (robot.y < 1000) {
        i = 0;
    } else if (robot.y < 1500) {
        i = 1;
    } else if (robot.y < 2000) {
        i = 2;
    }
    if (i != -1) {
        int dir = -1;
        if ((!is_sign[LEFT][i]) && (!is_sign[RIGHT][i])) {   
            if (i != 2) {
                if (is_sign[LEFT][i + 1]) {
                    dir = LEFT;
                } else if (is_sign[RIGHT][i + 1]) {
                    dir = RIGHT;
                }
            }
        } else {
            dir = is_sign[LEFT][i] ? LEFT : RIGHT;
        }
        if (dir != -1) {
            if (dir == side_move_forward) {
                target_distance = middle_target_distance + DIST_EVASION;
            } else {
                target_distance = middle_target_distance - DIST_EVASION;
            }
        }
    }
}

// Solving the task
void solve() {
    motorWrite(170);
    moveStart();
    rotate();
    for (int i = 0; i < 11; ++i) {
        moveToRotate();
        rotate();
    }
    moveFinish();
    
    
    motorStop();
    lidarStop();
}

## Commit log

2021-06-21 Add Mk. I and Mk. II versions
    [Arduino UNO.0003.ipt, Arduino UNO.ipt, Encoder.0001.ipt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]
2021-06-25 Fix model
    [Втулка между подшипниками рулевого управления.0002.ipt, Втулка между подшипниками рулевого управления.0003.ipt, Втулка между подшипниками рулевого управления.i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]
2021-06-26 Add back rear mounts for ultrasonics
    [Крепление ультрасоника заднее.0001.ipt, Крепление ультрасоника заднее.ipt]
2021-06-28 Add robot stand
    [Крепление USB.0001.ipt, Крепление USB.ipt, Крепление дифференциала.0008.ipt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]
2021-08-09 Add new versions
    [1.25 2pin-1.ipt, 1.25 2pin-2.ipt, 1.25 3pinb͹.ipt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]
2021-09-05 Add new models and fix bugs
    [ESP32 LOLIN32 V1.0.0.0001.ipt, ESP32 LOLIN32 V1.0.0.0003.ipt, ESP32 LOLIN32 V1.0.0.ipt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]
2021-09-24 Add new models
    [1.25 2pin-1.ipt, 1.25 2pin-2.ipt, 1.25 3pinb͹.ipt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]
2021-09-24 Add more models
    [1.25 3pinb.ipt, 1.25 3pinb͹.ipt, RPLIDAR A1M8.0006.iam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]
2021-10-11 Add new gear
    [RPLIDAR A1M8.0010.iam, RPLIDAR A1M8.0011.iam, RPLIDAR A1M8.iam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]
2021-10-11 change about sensor
2021-10-11 Add new description
    [Колесо D40 под планшайбу.0003.ipt, Колесо D40 под планшайбу.0004.ipt, Колесо D40 под планшайбу.ipt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]
2021-10-11 Removing the superfluous
    [Ведущая шестерня дифференециала 24.stl, Ведущая шестерня дифференециала.stl, Деталь крепления диска к поворотному механизму.stl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]
2022-06-29 add 3d models
    [rro.f3d, rro.step, дно.stl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]
2022-06-29 Welcome back Violet
    [1.25 2pin-1.ipt, 1.25 2pin-2.ipt, 1.25 3pinb.ipt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]
2022-07-01 Welcome back MicRobot!
    [1.25 2pin-1.ipt, 1.25 2pin-2.ipt, 1.25 3pinb.ipt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]
2022-07-01 Add some correction
    [1.25 2pin-1.ipt, 1.25 2pin-2.ipt, 1.25 3pinb.ipt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]
2022-07-02 Revert "Add new models"
    This reverts commit 247424d33f57ae208985a60124670692a8a39939.
    [1.25 2pin-1.ipt, 1.25 2pin-2.ipt, 1.25 3pinb.ipt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]
2022-07-03 Add correct to the code
    [_geoma_objects.ino, main.ino]
